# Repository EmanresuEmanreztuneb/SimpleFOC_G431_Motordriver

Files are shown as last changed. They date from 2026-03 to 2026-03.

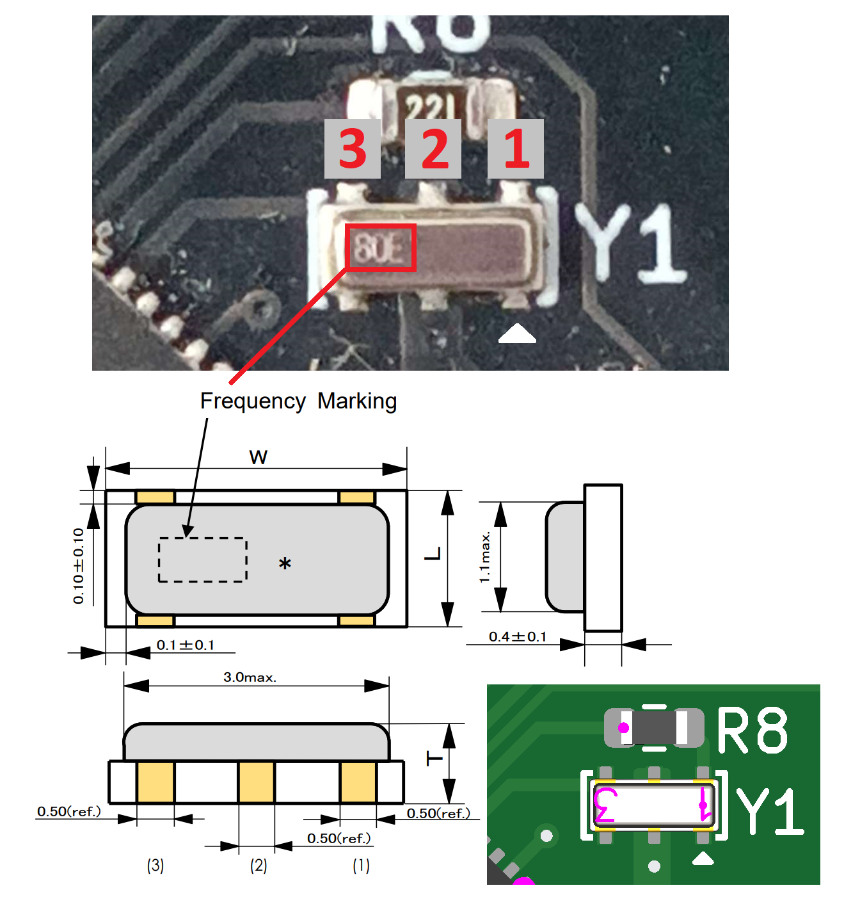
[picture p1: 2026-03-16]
Pics/Oscillator placing.png

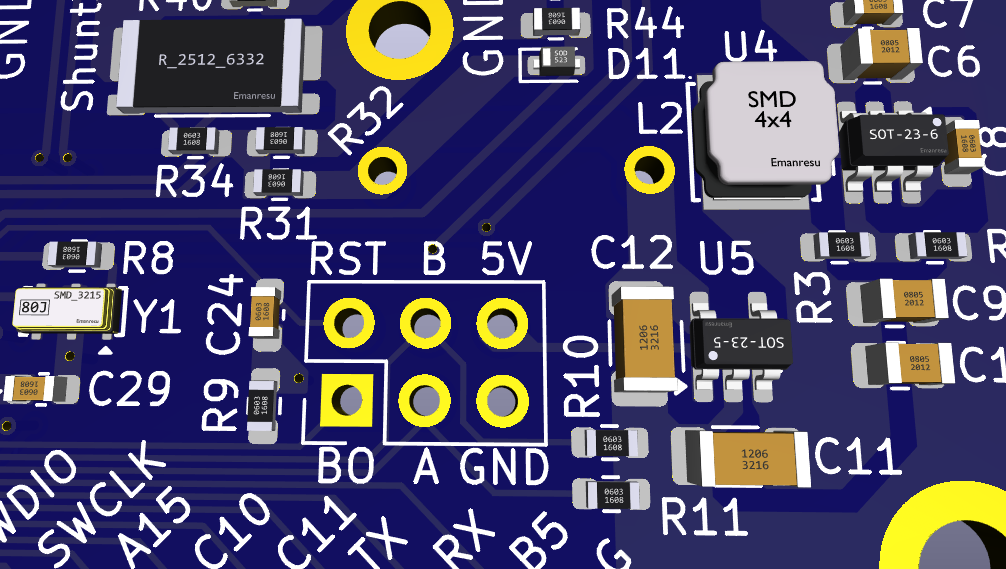
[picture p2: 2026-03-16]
Pics/CAD_Models.PNG

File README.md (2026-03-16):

# SimpleFOC_G431_Motordriver (24V version)
A motordriver based in STM's G431 Drone ESC

Reason to create it was mainly because of the poor thermal performance of the original development board.
Now the whole "layer sandwich" is gone and every existing active layer can breath fresh air.

Changes:

<ins>**Two layer**</ins> <br>
&nbsp;&nbsp;&nbsp;&nbsp;&nbsp;&nbsp;&nbsp;&nbsp;As mentioned, the layer count has been reduced from eight to just two.<br>
&nbsp;&nbsp;&nbsp;&nbsp;&nbsp;&nbsp;&nbsp;&nbsp;The KiCad files still include two "blind" internal layers between top<br>
&nbsp;&nbsp;&nbsp;&nbsp;&nbsp;&nbsp;&nbsp;&nbsp;and bottom to test whether additional shielding makes a difference.<br>
&nbsp;&nbsp;&nbsp;&nbsp;&nbsp;&nbsp;&nbsp;&nbsp;to test if the additional shielding makes any difference.<br>
&nbsp;&nbsp;&nbsp;&nbsp;&nbsp;&nbsp;&nbsp;&nbsp;Spoiler: It doesn’t...<br>
&nbsp;&nbsp;&nbsp;&nbsp;&nbsp;&nbsp;&nbsp;&nbsp;You can remove these layers if you plan to etch the PCB at home.<br> 
&nbsp;&nbsp;&nbsp;&nbsp;&nbsp;&nbsp;&nbsp;&nbsp;However, since the price at JLC remains nearly the same, I left them in.<br>
&nbsp;&nbsp;&nbsp;&nbsp;&nbsp;&nbsp;&nbsp;&nbsp;Adding them later would be more effort than simply removing them now.<br>

<ins>**Pins**</ins> <br>
&nbsp;&nbsp;&nbsp;&nbsp;&nbsp;&nbsp;&nbsp;&nbsp;To maintain the required dimensions while sticking to a two-layer design,<br>
&nbsp;&nbsp;&nbsp;&nbsp;&nbsp;&nbsp;&nbsp;&nbsp;I unfortunately had to remove the thermal sensor and LEDs.<br>
&nbsp;&nbsp;&nbsp;&nbsp;&nbsp;&nbsp;&nbsp;&nbsp;But you get new pins for your own modifications. (PA15, C10, C11, B5)<br>

<ins>**Stable 24V**</ins> <br>
&nbsp;&nbsp;&nbsp;&nbsp;&nbsp;&nbsp;&nbsp;&nbsp;On the original version, 24V operation was borderline and carried a high<br>
&nbsp;&nbsp;&nbsp;&nbsp;&nbsp;&nbsp;&nbsp;&nbsp;risk of component failure.<br>
&nbsp;&nbsp;&nbsp;&nbsp;&nbsp;&nbsp;&nbsp;&nbsp;The current design uses the LMR23630 for the first stage (VCC to 10V),<br>
&nbsp;&nbsp;&nbsp;&nbsp;&nbsp;&nbsp;&nbsp;&nbsp;which safely handles up to 36V.<br>
&nbsp;&nbsp;&nbsp;&nbsp;&nbsp;&nbsp;&nbsp;&nbsp;A 60V version is also planned; this will require upgrading to an LMR51635<br>
&nbsp;&nbsp;&nbsp;&nbsp;&nbsp;&nbsp;&nbsp;&nbsp;and adjusting the VCC sense resistors.<br>

<ins>**BOOT / Encoder**</ins> <br>
&nbsp;&nbsp;&nbsp;&nbsp;&nbsp;&nbsp;&nbsp;&nbsp;In the previous version, the BOOT pin (PB8) was used for Encoder Z with a<br>
&nbsp;&nbsp;&nbsp;&nbsp;&nbsp;&nbsp;&nbsp;&nbsp;pull-up and capacitor. This could cause startup issues, as the system <br>
&nbsp;&nbsp;&nbsp;&nbsp;&nbsp;&nbsp;&nbsp;&nbsp;relies on the capacitor's charging time to keep PB8 low during boot.<br>

&nbsp;&nbsp;&nbsp;&nbsp;&nbsp;&nbsp;&nbsp;&nbsp;The new design uses pull-downs without capacitors. This drops support for <br>
&nbsp;&nbsp;&nbsp;&nbsp;&nbsp;&nbsp;&nbsp;&nbsp;open-collector encoders, but standard models (AMS, CUI, MT6835, MT6701) <br>
&nbsp;&nbsp;&nbsp;&nbsp;&nbsp;&nbsp;&nbsp;&nbsp;work flawlessly.<br>

<ins>**ToDo**</ins> <br>
&nbsp;&nbsp;&nbsp;&nbsp;&nbsp;&nbsp;&nbsp;&nbsp;Current-sense gain requires a surprisingly high value to match real-world<br>
&nbsp;&nbsp;&nbsp;&nbsp;&nbsp;&nbsp;&nbsp;&nbsp;measurements. ->>> Investigating the root cause.<br>

Foto_01
Foto_02


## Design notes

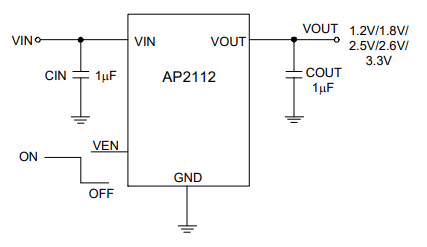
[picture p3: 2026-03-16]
Pics/AP2112.PNG

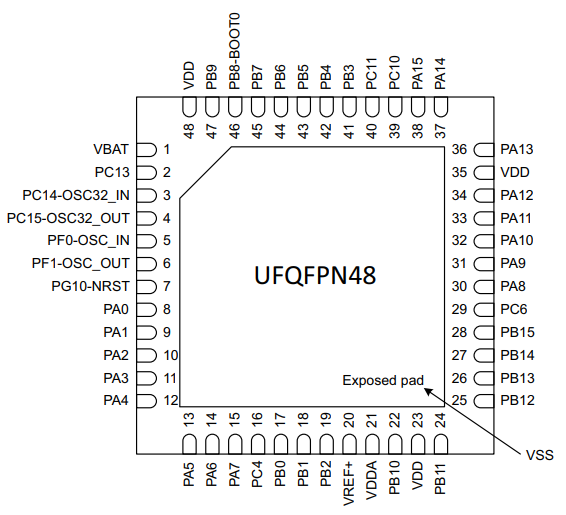
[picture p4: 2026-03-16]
Pics/STM32 G431 UFQFPN48.png

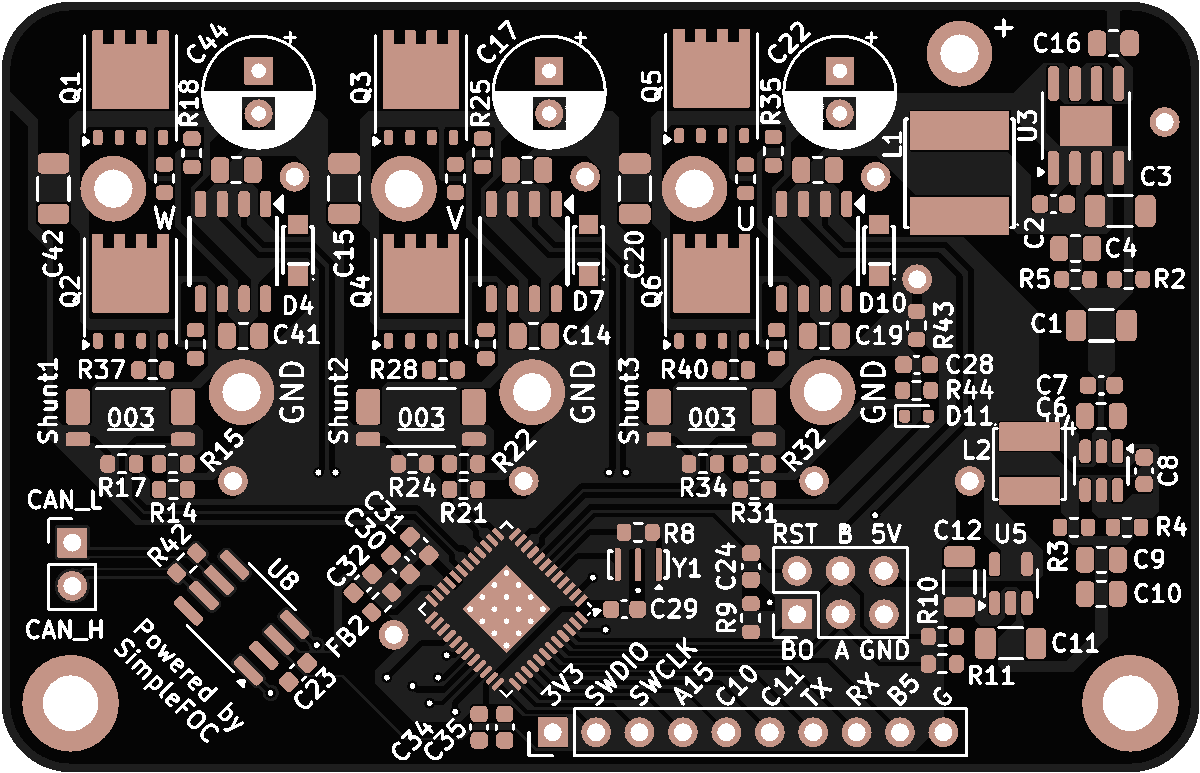
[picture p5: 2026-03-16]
Pics/sm_black_top.png

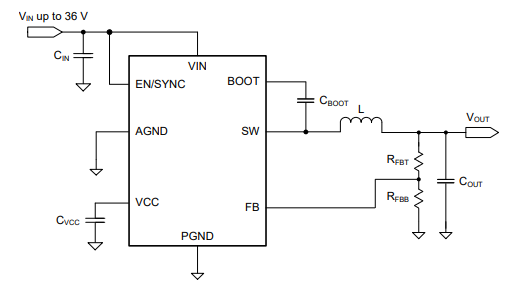
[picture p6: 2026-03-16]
Pics/LMR23630.PNG

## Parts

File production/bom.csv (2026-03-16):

Designator | Footprint | Quantity | Value | LCSC Part #
C1 | 1206 | 1 | 47μF/25V | C76659
C10, C9 | 0805 | 2 | 22μF/25V | C45783
C11, C12 | 1206 | 2 | 10μF/25V | C13585
C14, C16, C19, C41, C43, C45, C46, C6 | 0805 | 8 | 10μF/25V | C15850
C15, C20, C3, C42 | 1206 | 4 | 2.2μF/50V | C50254
C17, C22, C44 | CP_Radial_D6.3mm_P2.50mm | 3 | 47μF/50V | C45100
C2, C23, C24, C28, C29, C32, C7, C8 | 0603 | 8 | 100nF/50V | C14663
C30 | 0603 | 1 | 1μF/50V | C15849
C31, C35 | 0603 | 2 | 10nF/50V | C100042
C34 | 0603 | 1 | 4.7uF/25V | C69335
C4 | 0805 | 1 | 22pF/50V | C105623
D10, D4, D7 | FR107_SOD-123_L2.8-W1.8-LS3.7-RD-3 | 3 | FR107 | C3018495
D11 | D_SOD-523 | 1 | D_Schottky | C2926449
FB2 | 0603 | 1 | 600Ω@100MHz | C1002
L1 | INDUCTOR-SMD_L6.0-W6.0 | 1 | 18µH 106mOhm | C467143
L2 | INDUCTOR-SMD_L4.0-W4.0 | 1 | 15µH | C340394
Q1, Q2, Q3, Q4, Q5, Q6 | TDSON-8-1 | 6 | BSC026N08NS5 | C5955453
R10, R11, R20, R27, R28, R37, R39, R40, R9 | 0603 | 9 | 10K | C25804
R14, R21, R31 | 0603 | 3 | 22K | C31850
R15, R22, R32 | 0603 | 3 | 2K2 | C4190
R17, R24, R34 | 0603 | 3 | 1K5 | C2907083
R18, R19, R25, R26, R35, R36 | 0603 | 6 | 10 | C22859
R2 | 0603 | 1 | 22K1 | C137768
R3 | 0603 | 1 | 100K | C25803
R4 | 0603 | 1 | 13.3K | C25952
R42 | 0603 | 1 | 120 | C22787
R43 | 0603 | 1 | 169K | C22817
R44 | 0603 | 1 | 18K | C25810
R5 | 0603 | 1 | 200K | C25811
R8 | 0603 | 1 | 220 | C22962
SHUNT1, SHUNT2, SHUNT3 | R_Shunt_WSK2512_6332Metric_T1.19mm | 3 | R003 | C5375459
U1 | STM32 G431 QFN-48-1EP_7x7mm | 1 | STM32G431_UFQFPN48 | C529356
U11, U6, U9 | EG3112_IRS | 3 | EG3112 | C111908
U3 | SOIC-8-1EP_3.9x4.9mm_P1.27mm_EP2.29x3mm | 1 | LMR23630 | C601653
U4 | SOT-23-6 | 1 | TPS54202DDCR | C191884
U5 | SOT-23-5 | 1 | AP2112K-3.3 | C51118
U8 | SOIC-8_3.9x4.9mm_P1.27mm | 1 | SN65HVD232DR | C30530
Y1 | CSTNE8M00GH5C000R0 | 1 | 8Mhz | C341525

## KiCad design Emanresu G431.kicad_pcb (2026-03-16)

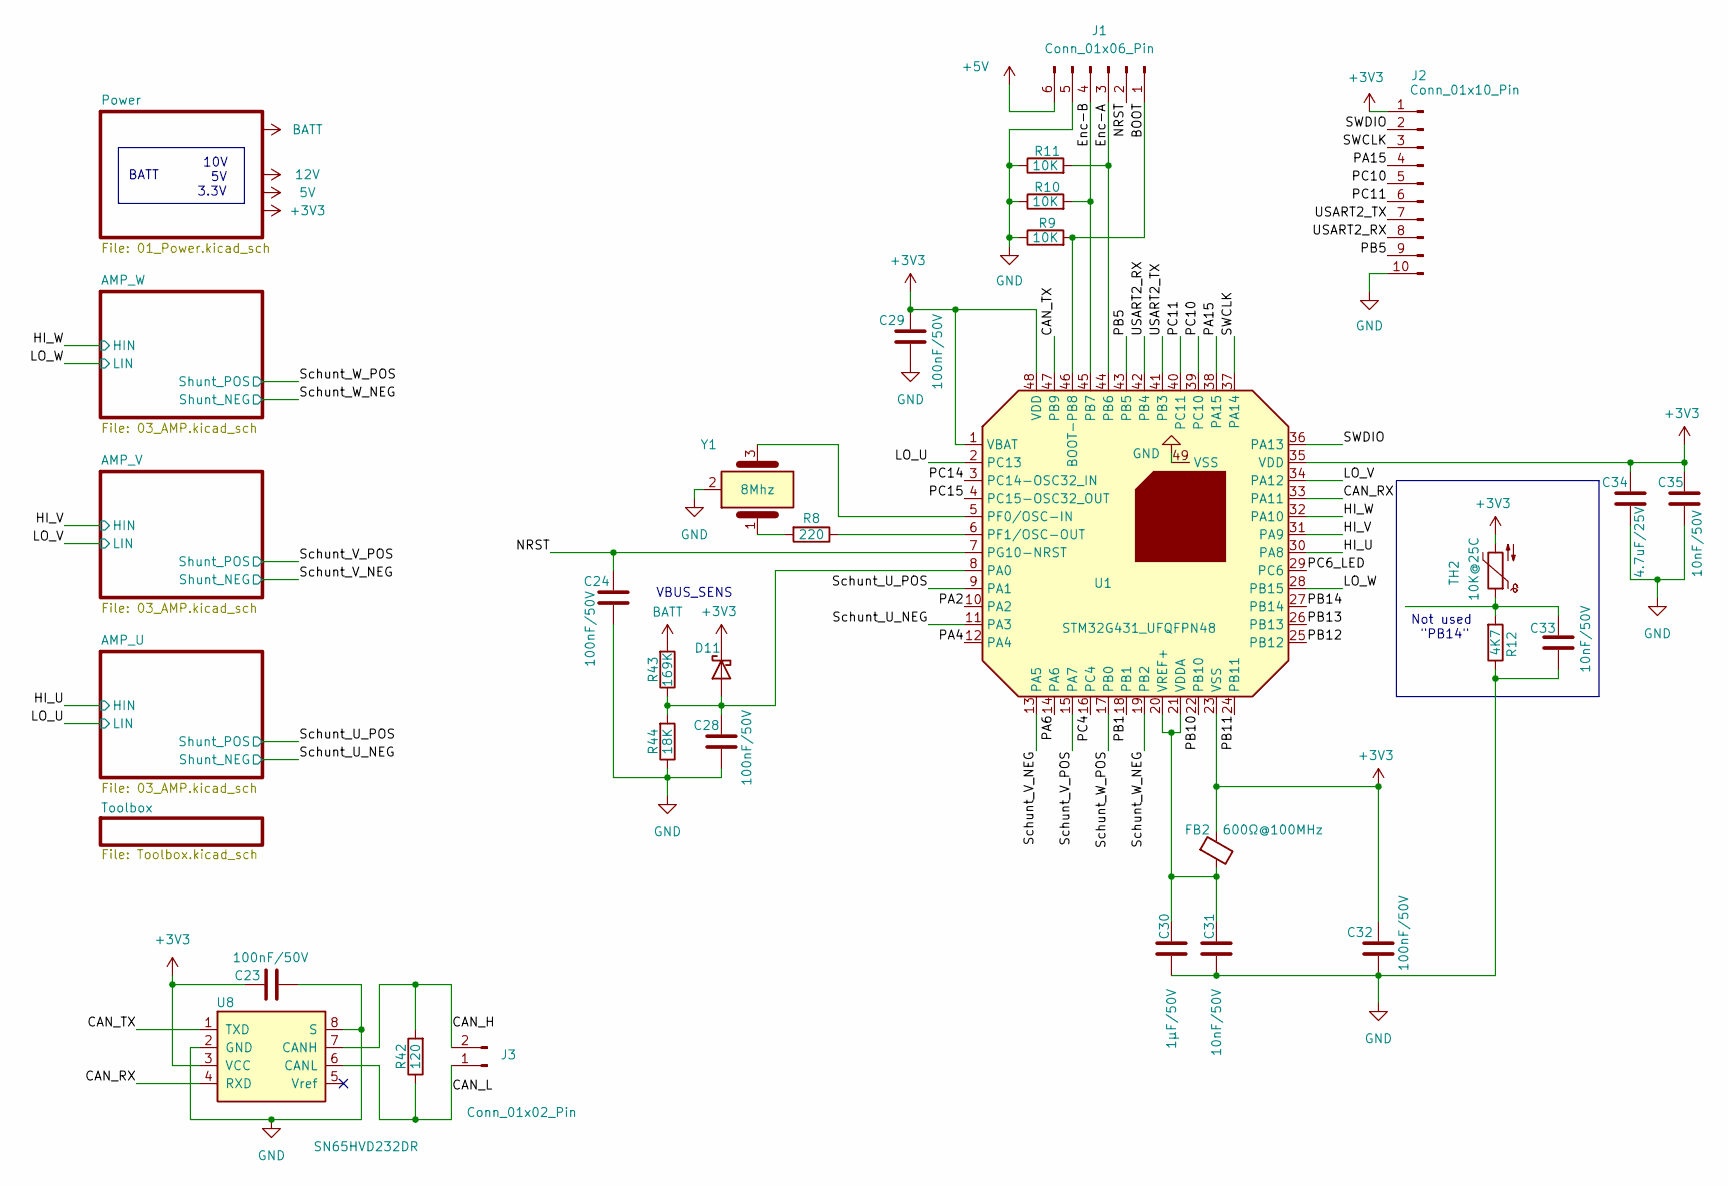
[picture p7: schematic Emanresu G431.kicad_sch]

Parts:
C23, C24, C28, C29, C32: 100nF/50V; C_0603_1608Metric; LCSC C14663
C30: 1μF/50V; C_0603_1608Metric; LCSC C15849
C31, C33, C35: 10nF/50V; C_0603_1608Metric; LCSC C100042
C34: 4.7uF/25V; C_0603_1608Metric; LCSC C69335
D11: D_Schottky; D_SOD-523; LCSC C2926449
FB2: 600Ω@100MHz; R_0603_1608Metric; LCSC C1002
J1: Conn_01x06_Pin; PinHeader_2x03_P2.54mm_Vertical
J2: Conn_01x10_Pin; PinHeader_1x10_P2.54mm_Vertical
J3: Conn_01x02_Pin; PinHeader_1x02_P2.54mm_Vertical
R8: 220; R_0603_1608Metric; LCSC C22962
R9, R10, R11: 10K; R_0603_1608Metric; LCSC C25804
R12: 4K7; R_0603_1608Metric; JLCPCB C23162
R42: 120; R_0603_1608Metric; LCSC C22787
R43: 169K; R_0603_1608Metric; LCSC C22817
R44: 18K; R_0603_1608Metric; LCSC C25810
TH2: 10K@25C; R_0603_1608Metric; JLCPCB C13564
U1: STM32G431_UFQFPN48; STM32 G431 QFN-48-1EP_7x7mm; LCSC C529356
U8: SN65HVD232DR; SOIC-8_3.9x4.9mm_P1.27mm; LCSC C30530
Y1: 8Mhz; CSTNE8M00GH5C000R0; LCSC C341525

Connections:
+3V3: C23.2, C29.2, C32.2, C34.2, C35.2, D11.1 (K), FB2.1, J2.1, TH2.2, U1.1 (VBAT), U1.23 (VSS), U1.35 (VDD), U1.48 (VDD), U8.3 (VCC); also elsewhere on the board
+5V: J1.6; also elsewhere on the board
/BOOT: J1.1, R9.2, U1.46 (BOOT-PB8)
/CAN_H: J3.2, R42.2, U8.7 (CANH)
/CAN_L: J3.1, R42.1, U8.6 (CANL)
/CAN_RX: U1.33 (PA11), U8.4 (RXD)
/CAN_TX: U1.47 (PB9), U8.1 (TXD)
/Enc-A: J1.3, R11.2, U1.44 (PB6)
/Enc-B: J1.4, R10.2, U1.45 (PB7)
/HI_U: U1.30 (PA8); also elsewhere on the board
/HI_V: U1.31 (PA9); also elsewhere on the board
/HI_W: U1.32 (PA10); also elsewhere on the board
/LO_U: U1.2 (PC13); also elsewhere on the board
/LO_V: U1.34 (PA12); also elsewhere on the board
/LO_W: U1.28 (PB15); also elsewhere on the board
/NRST: C24.2, J1.2, U1.7 (PG10-NRST)
/PA2: U1.10 (PA2)
/PA4: U1.12 (PA4)
/PA6: U1.14 (PA6)
/PA15: J2.4, U1.38 (PA15)
/PB1: U1.18 (PB1)
/PB5: J2.9, U1.43 (PB5)
/PB10: U1.22 (PB10)
/PB11: U1.24 (PB11)
/PB12: U1.25 (PB12)
/PB13: U1.26 (PB13)
/PB14: U1.27 (PB14)
/PC4: U1.16 (PC4)
/PC6_LED: U1.29 (PC6)
/PC10: J2.5, U1.39 (PC10)
/PC11: J2.6, U1.40 (PC11)
/PC14: U1.3 (PC14-OSC32_IN)
/PC15: U1.4 (PC15-OSC32_OUT)
/SWCLK: J2.3, U1.37 (PA14)
/SWDIO: J2.2, U1.36 (PA13)
/Schunt_U_NEG: U1.11 (PA3); also elsewhere on the board
/Schunt_U_POS: U1.9 (PA1); also elsewhere on the board
/Schunt_V_NEG: U1.13 (PA5); also elsewhere on the board
/Schunt_V_POS: U1.15 (PA7); also elsewhere on the board
/Schunt_W_NEG: U1.19 (PB2); also elsewhere on the board
/Schunt_W_POS: U1.17 (PB0); also elsewhere on the board
/USART2_RX: J2.8, U1.42 (PB4)
/USART2_TX: J2.7, U1.41 (PB3)
BATT: R43.2; also elsewhere on the board
GND: C23.1, C24.1, C28.1, C29.1, C30.1, C31.1, C32.1, C33.1, C34.1, C35.1, J1.5, J2.10, R9.1, R10.1, R11.1, R12.1, R44.1, U1.49 (VSS), U8.2 (GND), U8.8 (S), Y1.2; also elsewhere on the board
unnamed: C33.2, R12.2, TH2.1
unnamed: C28.2, D11.2 (A), R43.1, R44.2, U1.8 (PA0)
unnamed: R8.2, Y1.1
unnamed: U1.5 (PF0/OSC-IN), Y1.3
unnamed: R8.1, U1.6 (PF1/OSC-OUT)
unnamed: C30.2, C31.2, FB2.2, U1.20 (VREF+), U1.21 (VDDA)

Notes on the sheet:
10V 5V 3.3V
BATT
Not used "PB14"
VBUS_SENS

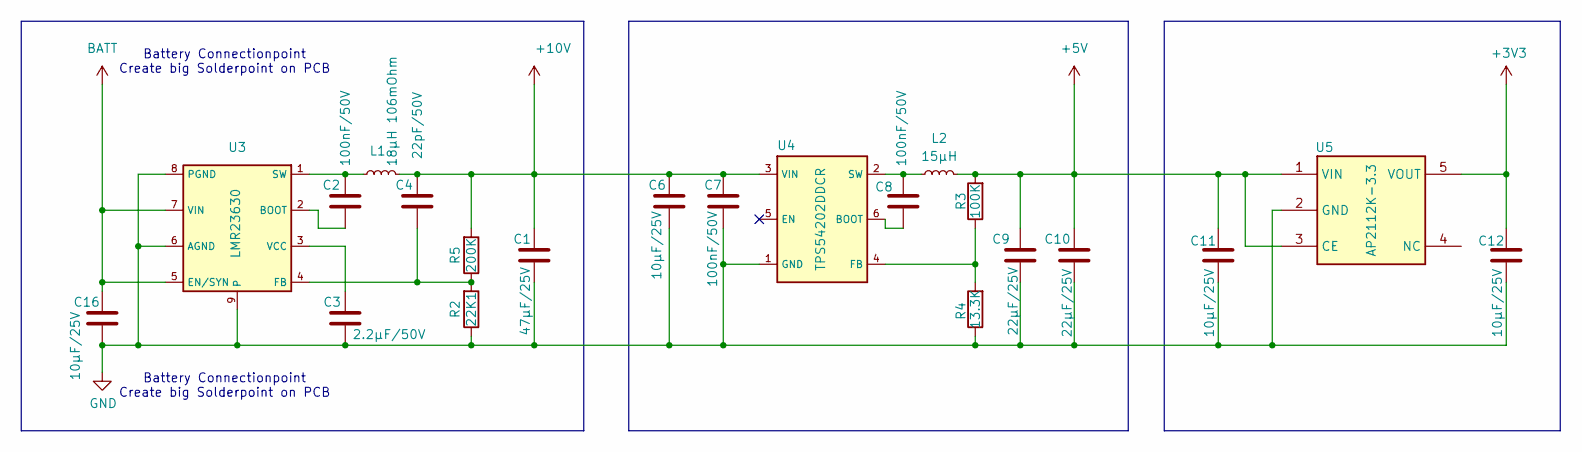
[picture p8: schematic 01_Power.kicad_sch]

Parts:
C1: 47μF/25V; C_1206_3216Metric; LCSC C76659
C2, C7, C8: 100nF/50V; C_0603_1608Metric; LCSC C14663
C3: 2.2μF/50V; C_1206_3216Metric; Part Number CL31B225KBHVPNE; Digikey 1276-6735-1-ND
C4: 22pF/50V; C_0805_2012Metric; LCSC C105623
C6, C16: 10μF/25V; C_0805_2012Metric; LCSC C15850
C9, C10: 22μF/25V; C_0805_2012Metric; LCSC C45783
C11, C12: 10μF/25V; C_1206_3216Metric; LCSC C13585
L1: 18µH 106mOhm; INDUCTOR-SMD_L6.0-W6.0; LCSC C467143
L2: 15µH; INDUCTOR-SMD_L4.0-W4.0; LCSC C340394
R2: 22K1; R_0603_1608Metric; LCSC C137768
R3: 100K; R_0603_1608Metric; LCSC C25803
R4: 13.3K; R_0603_1608Metric; LCSC C25952
R5: 200K; R_0603_1608Metric; LCSC C25811
U3: LMR23630; SOIC-8-1EP_3.9x4.9mm_P1.27mm_EP2.29x3mm; LCSC C601653
U4: TPS54202DDCR; SOT-23-6; LCSC C191884
U5: AP2112K-3.3; SOT-23-5; LCSC C51118

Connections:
+3V3: C12.1, U5.5 (VOUT); also elsewhere on the board
+5V: C9.1, C10.1, C11.1, L2.2, R3.2, U5.1 (VIN), U5.3 (CE); also elsewhere on the board
+10V: C1.1, C4.1, C6.1, C7.1, L1.1, R5.2, U4.3 (VIN); also elsewhere on the board
BATT: C16.2, U3.5 (EN/SYN), U3.7 (VIN); also elsewhere on the board
GND: C1.2, C3.2, C6.2, C7.2, C9.2, C10.2, C11.2, C12.2, C16.1, R2.1, R4.1, U3.6 (AGND), U3.8 (PGND), U3.9, U4.1 (GND), U5.2 (GND); also elsewhere on the board
unnamed: C2.1, U3.2 (BOOT)
unnamed: C4.2, R2.2, R5.1, U3.4 (FB)
unnamed: C2.2, L1.2, U3.1 (SW)
unnamed: C3.1, U3.3 (VCC)
unnamed: C8.2, U4.6 (BOOT)
unnamed: R3.1, R4.2, U4.4 (FB)
unnamed: C8.1, L2.1, U4.2 (SW)

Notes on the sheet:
Battery Connectionpoint Create big Solderpoint on PCB

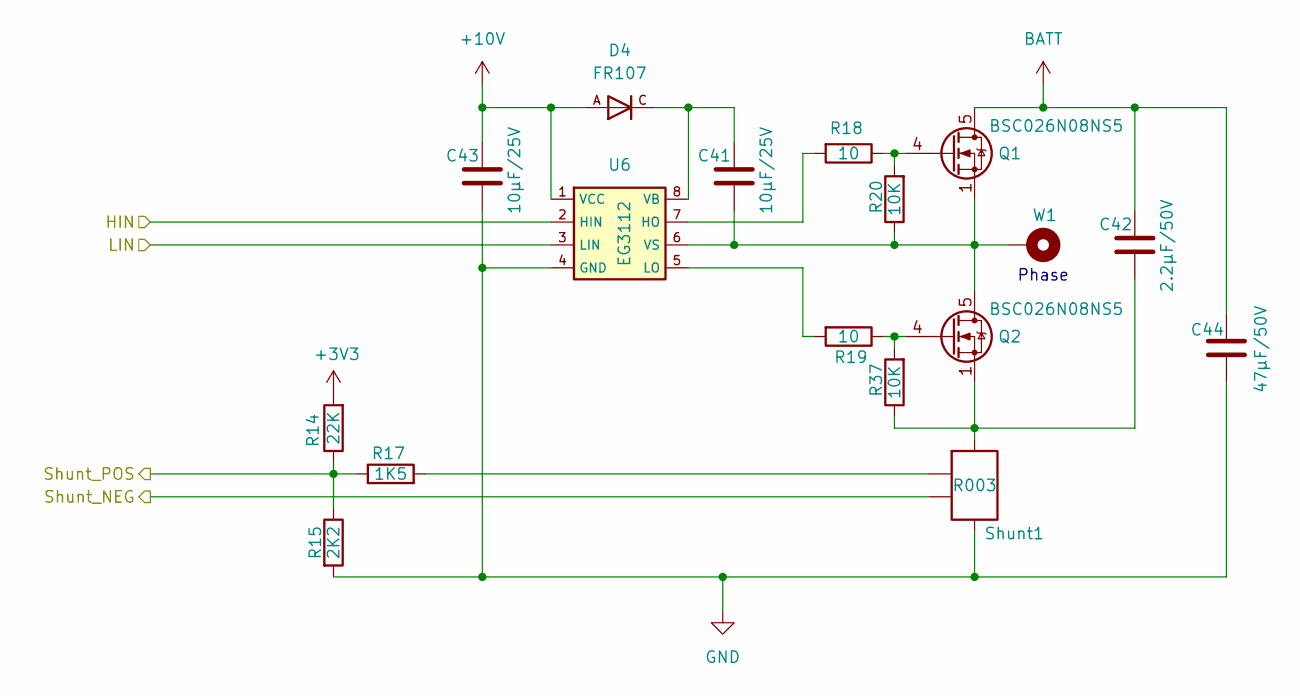
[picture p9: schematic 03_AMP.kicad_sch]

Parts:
C41, C43: 10μF/25V; C_0805_2012Metric; LCSC C15850
C42: 2.2μF/50V; C_1206_3216Metric; LCSC C50254
C44: 47μF/50V; CP_Radial_D6.3mm_P2.50mm; LCSC C45100
D4: FR107; FR107_SOD-123_L2.8-W1.8-LS3.7-RD-3; LCSC C3018495
Q1, Q2: BSC026N08NS5; TDSON-8-1; LCSC C5955453
R14: 22K; R_0603_1608Metric; LCSC C31850
R15: 2K2; R_0603_1608Metric; LCSC C4190
R17: 1K5; R_0603_1608Metric; LCSC C2907083
R18, R19: 10; R_0603_1608Metric; LCSC C22859
R20, R37: 10K; R_0603_1608Metric; LCSC C25804
Shunt1: R003; R_Shunt_WSK2512_6332Metric_T1.19mm; LCSC C5375459
U6: EG3112; EG3112_IRS; LCSC C111908
W1: 2.2mm_Through_Connector

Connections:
+3V3: R14.2; also elsewhere on the board
+10V: C43.2, D4.A, U6.1 (VCC); also elsewhere on the board
/HI_W: U6.2 (HIN); also elsewhere on the board
/LO_W: U6.3 (LIN); also elsewhere on the board
/Schunt_W_NEG: Shunt1.2; also elsewhere on the board
/Schunt_W_POS: R14.1, R15.1, R17.1; also elsewhere on the board
BATT: C42.1, C44.1, Q1.5 (D); also elsewhere on the board
GND: C43.1, C44.2, R15.2, Shunt1.1, U6.4 (GND); also elsewhere on the board
unnamed: C42.2, Q2.1 (S), Q2.2 (S), Q2.3 (S), R37.1, Shunt1.4
unnamed: Q1.4 (G), R18.1, R20.2
unnamed: C41.1, Q1.1 (S), Q1.2 (S), Q1.3 (S), Q2.5 (D), R20.1, U6.6 (VS), W1.1
unnamed: Q2.4 (G), R19.1, R37.2
unnamed: R17.2, Shunt1.3
unnamed: R18.2, U6.7 (HO)
unnamed: R19.2, U6.5 (LO)
unnamed: C41.2, D4.C, U6.8 (VB)

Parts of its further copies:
C14, C19, C45, C46: 10μF/25V; C_0805_2012Metric; LCSC C15850
C15, C20: 2.2μF/50V; C_1206_3216Metric; LCSC C50254
C17, C22: 47μF/50V; CP_Radial_D6.3mm_P2.50mm; LCSC C45100
D7, D10: FR107; FR107_SOD-123_L2.8-W1.8-LS3.7-RD-3; LCSC C3018495
Q3, Q4, Q5, Q6: BSC026N08NS5; TDSON-8-1; LCSC C5955453
R21, R31: 22K; R_0603_1608Metric; LCSC C31850
R22, R32: 2K2; R_0603_1608Metric; LCSC C4190
R24, R34: 1K5; R_0603_1608Metric; LCSC C2907083
R25, R26, R35, R36: 10; R_0603_1608Metric; LCSC C22859
R27, R28, R39, R40: 10K; R_0603_1608Metric; LCSC C25804
Shunt2, Shunt3: R003; R_Shunt_WSK2512_6332Metric_T1.19mm; LCSC C5375459
U2: 2.2mm_Through_Connector
U9, U11: EG3112; EG3112_IRS; LCSC C111908
V1: 2.2mm_Through_Connector

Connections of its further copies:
+3V3: R21.2, R31.2; also elsewhere on the board
+10V: C45.2, C46.2, D7.A, D10.A, U9.1 (VCC), U11.1 (VCC); also elsewhere on the board
/HI_U: U11.2 (HIN); also elsewhere on the board
/HI_V: U9.2 (HIN); also elsewhere on the board
/LO_U: U11.3 (LIN); also elsewhere on the board
/LO_V: U9.3 (LIN); also elsewhere on the board
/Schunt_U_NEG: Shunt3.2; also elsewhere on the board
/Schunt_U_POS: R31.1, R32.1, R34.1; also elsewhere on the board
/Schunt_V_NEG: Shunt2.2; also elsewhere on the board
/Schunt_V_POS: R21.1, R22.1, R24.1; also elsewhere on the board
BATT: C15.1, C17.1, C20.1, C22.1, Q3.5 (D), Q5.5 (D); also elsewhere on the board
GND: C17.2, C22.2, C45.1, C46.1, R22.2, R32.2, Shunt2.1, Shunt3.1, U9.4 (GND), U11.4 (GND); also elsewhere on the board
unnamed: C15.2, Q4.1 (S), Q4.2 (S), Q4.3 (S), R28.1, Shunt2.4
unnamed: C20.2, Q6.1 (S), Q6.2 (S), Q6.3 (S), R40.1, Shunt3.4
unnamed: Q3.4 (G), R25.1, R27.2
unnamed: C14.1, Q3.1 (S), Q3.2 (S), Q3.3 (S), Q4.5 (D), R27.1, U9.6 (VS), V1.1
unnamed: Q4.4 (G), R26.1, R28.2
unnamed: Q5.4 (G), R35.1, R39.2
unnamed: C19.1, Q5.1 (S), Q5.2 (S), Q5.3 (S), Q6.5 (D), R39.1, U2.1, U11.6 (VS)
unnamed: Q6.4 (G), R36.1, R40.2
unnamed: R24.2, Shunt2.3
unnamed: R34.2, Shunt3.3
unnamed: R25.2, U9.7 (HO)
unnamed: R26.2, U9.5 (LO)
unnamed: C14.2, D7.C, U9.8 (VB)
unnamed: R35.2, U11.7 (HO)
unnamed: R36.2, U11.5 (LO)
unnamed: C19.2, D10.C, U11.8 (VB)

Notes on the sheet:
Phase

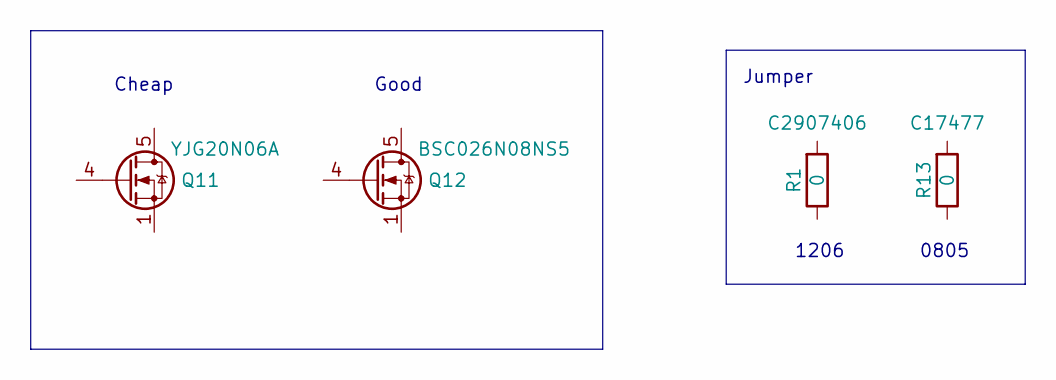
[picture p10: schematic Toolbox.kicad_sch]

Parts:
Q11: YJG20N06A; TDSON-8-1; JLC C919592
Q12: BSC026N08NS5; TDSON-8-1; JLC C5955453
R1: 0; R_1206_3216Metric; JLCPCB C2907406
R13: 0; R_0805_2012Metric; JLCPCB C17477

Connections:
unnamed: Q11.1 (S), Q11.2 (S), Q11.3 (S)
unnamed: Q12.1 (S), Q12.2 (S), Q12.3 (S)

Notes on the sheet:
1206
Good
Jumper
0805
Cheap

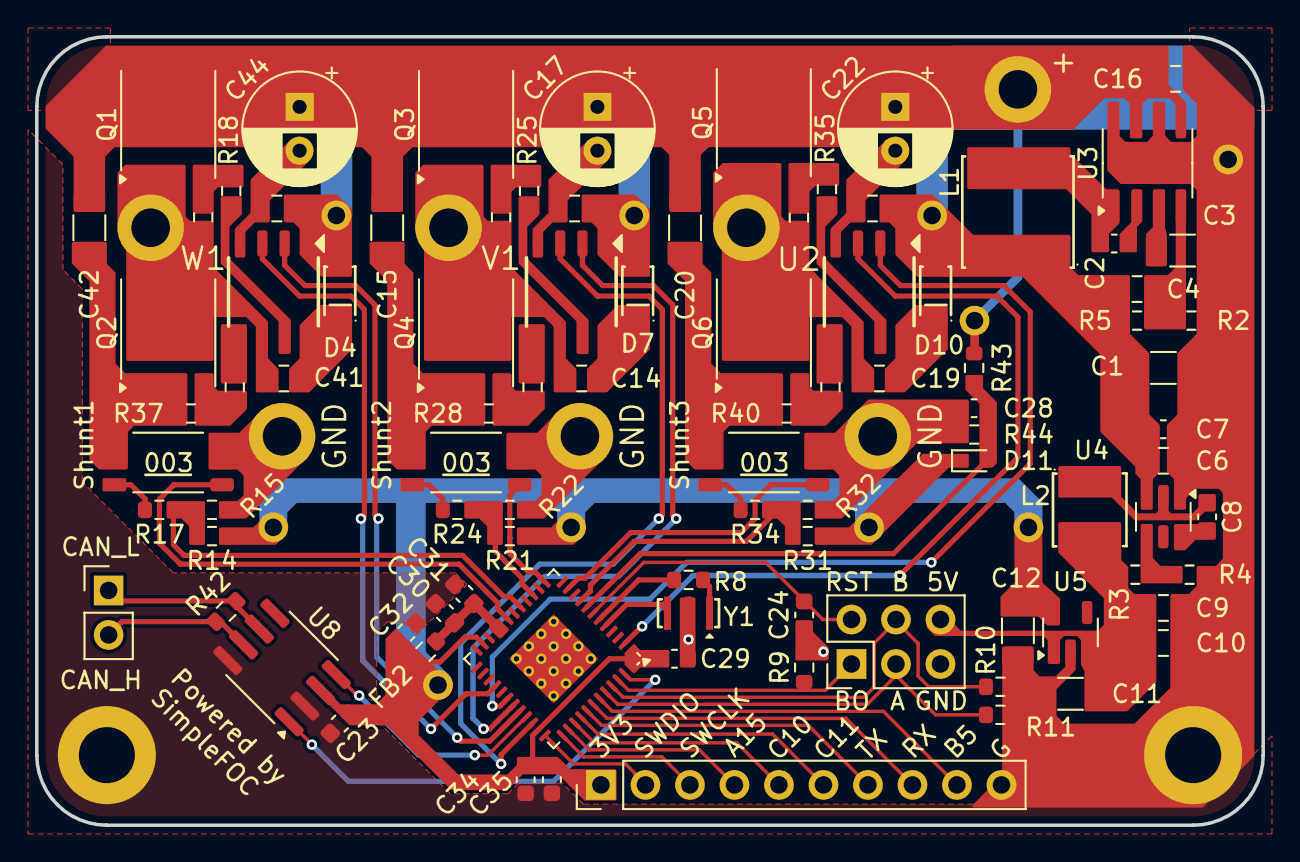
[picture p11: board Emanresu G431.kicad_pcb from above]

Board: 4 copper layers, 70.0 x 45.0 mm, 110 parts (0 on the bottom side), 69 nets.

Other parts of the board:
3V3, 3V3#2, 3V3#3, 3V3#4, 3V3#5, 10V, 10V#2, 10V#3: Single_Header_P2.54mm_Round
+: Val**; 2.2mm_Through_Connector
BATT: Single_Header_P2.54mm_Round
GND: Val**; 2.2mm_Through_Connector
GND#2, GND#3: Val**; 2.2mm_Through_Connector
J?: Single_Header_P2.54mm_Round

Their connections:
+3V3: 3V3.1, 3V3#2.1, 3V3#3.1, 3V3#4.1, 3V3#5.1; also elsewhere on the board
+10V: 10V.1, 10V#2.1, 10V#3.1; also elsewhere on the board
BATT: +.1, BATT.1; also elsewhere on the board
GND: GND.1, GND#2.1, GND#3.1, J?.1; also elsewhere on the board
